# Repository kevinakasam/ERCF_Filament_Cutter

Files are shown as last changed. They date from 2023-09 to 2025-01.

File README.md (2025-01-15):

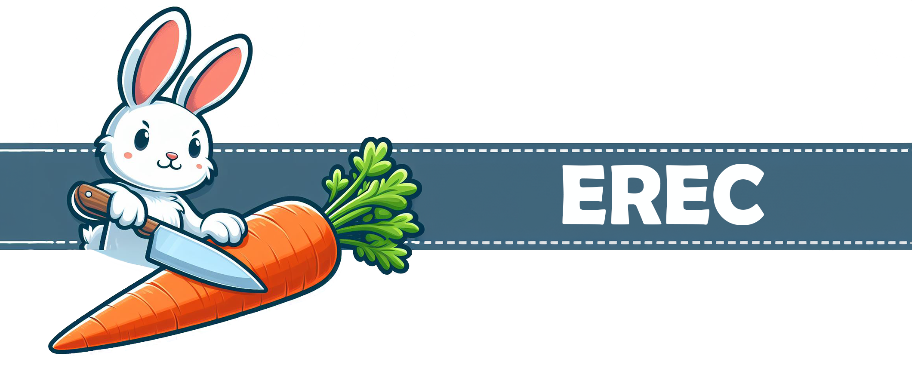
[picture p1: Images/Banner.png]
   

# Enraged Rabbit Encoder Cutter - Beta 7.0 🥕
<p align="center">
   &nbsp; 
   &nbsp;
   &nbsp;
</p>

### Attention! 
<strong> I’m not an expert and 3D printing is just my hobby. So please be careful when you build this mod and don’t just go ahead. All parts are tested and working. But everybody bears the risks of a modification him/herself! I'm not responsible if any harm occurs, so be careful, especially with the knife! </strong>

## Overview 

**[EREC](#erec)**<br>
**[BOM](#bom)**<br>
**[Assembly](#assembly)**<br>
**[Firmware](#firmware)**<br>
**[Changelog](#changelog--archive)**<br>
**[Showroom](#Showroom)**<br>
**[Acknowledgements](#Acknowledgements)**<br>

## EREC

This is a simple filament cutter for the awesome ERCF so tip tuning is less important.

It's made out of a Servo and a scalpell/exacto knife blade. The cutter get's mouted to the selector chart just behind the encoder - the cutter is basically an arm that swings to the left and right. Since the ECAS sits now on the Arm the filament path can be opened by swining the arm to the side. Then the ERCF can feed some filament mid air (*the filament tip*) and when the arm swings back to close the filament path the tip gets cut off by the knife on the arm. The cut off tip just falls off to the ground and the filament can be loaded with a clean tip the next time.

#### Why?
I never thought about a filament cutter untill I saw the [Filametrix](https://github.com/sorted01/Filametrix) design / got it recommended. Since I'm not using the ERCF with a Stealthburner (for now at least) I would have to make a cutter on my own. At the same time u/[BioKeks](https://github.com/BioCookieYT) requested a cutter for my Ender 3 fan duct ([Frankenstein 2.0](https://github.com/kevinakasam/FrankEnstein-Duct/tree/main/Frank2.0_Beta)) and that way I though we need something universial. After some days of tinkering this was the result - first with the MG90s servo, but that was so weak it was far aways from cutting it. So long speech short, thanks to [sorted01](https://github.com/sorted01) for the idea with the cutter!

#### Current Status
Considering my other ongoing [projects](https://kevinakasam.com/), I’ve decided to appoint u/[BioKeks](https://github.com/BioCookieYT) as the new primary contributor to this project. Don’t worry, I’m not completely stepping away, but if you have any questions, feel free to ask u/[BioKeks](https://github.com/BioCookieYT)!
<br>
<br>
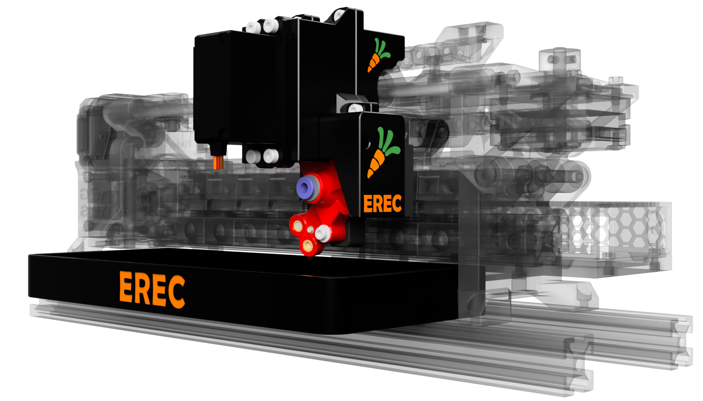
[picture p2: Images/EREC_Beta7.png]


## BOM
<table>
<tr>
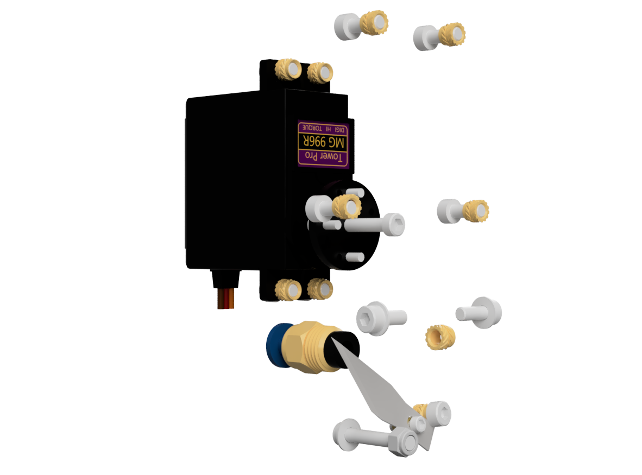
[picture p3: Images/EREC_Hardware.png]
EREC_Hardware
<td width=25%></td>
<td>
You can find the EREC BOM here. Make sure to gather all the required hardware before starting the assembly process ;)
<p>

[BOM](Doc/BOM.md) 
</td>
</tr>
</table>
<br>

## Assembly 

<table>
<tr>
<td>
The assembly process is straightforward; I’ve tried my best to keep it simple. If you need any help, feel free to join our discord server. 
<p>

[Documentation](Doc/EREC_BETA7.pdf) &nbsp;&nbsp; [Discord Server](https://discord.gg/Jw4frr64yV) &nbsp;&nbsp; [Discord Channel Link](https://discord.com/channels/964441223169449984/1169733100700434543)
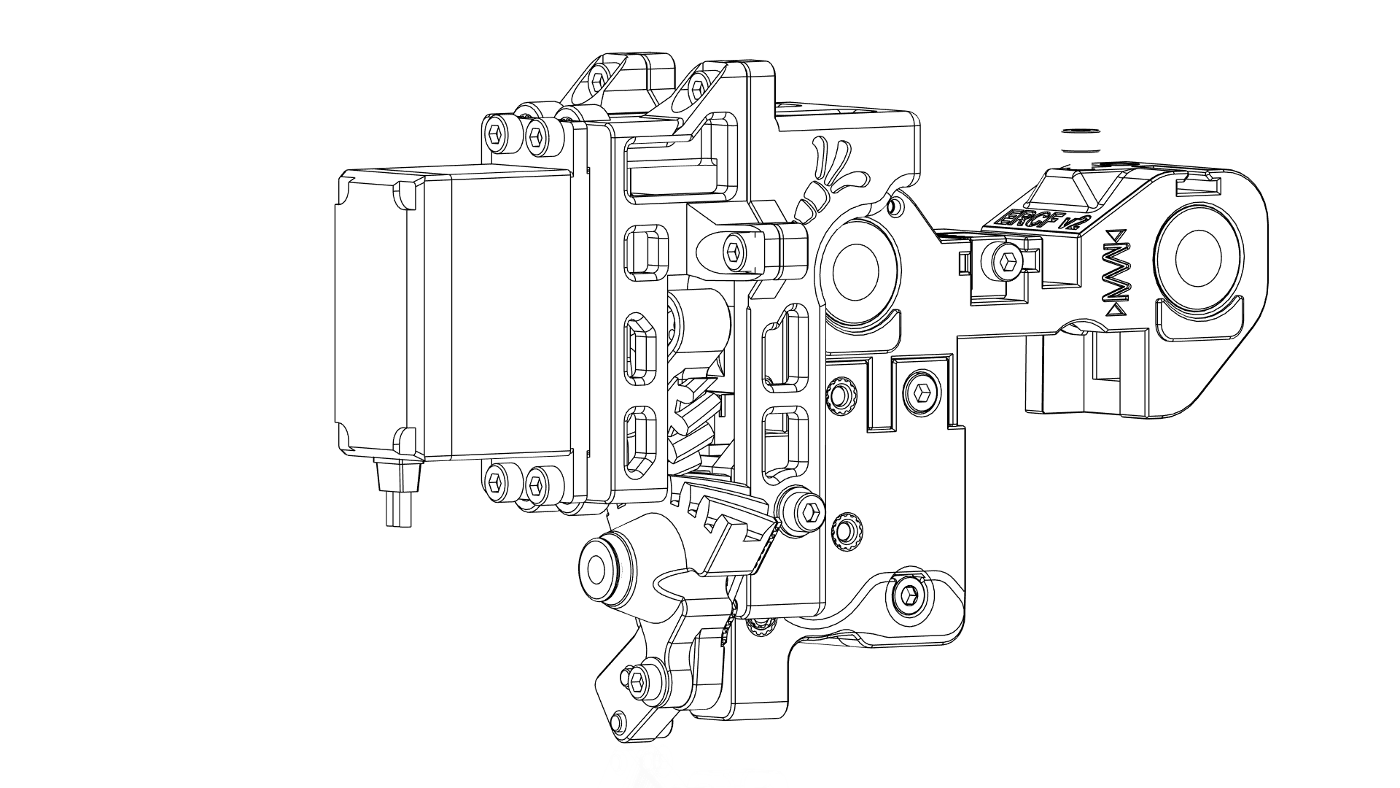
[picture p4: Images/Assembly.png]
<td width=35%></td>
</td>

</tr>
</table>

<br>

## Firmware
<table>
<tr>
<td width=20%>KlipperScreen</td>
<td>
EREC uses HappyHareV2 as its firmware. Thanks to maggieuk, you can enjoy easy integration as a third-party addon. For people using still ERCF-Software-V3, you can try the fork from u/ntchris. 

 [Happy Hare](https://github.com/moggieuk/Happy-Hare/wiki/Addon-Feature-Setup#---erec-filament-cutter) &nbsp;&nbsp; [ERCF-Software-V3 Fork](https://github.com/ntchris/ERCF-Software-V3)
</td>
</tr>
</table>

<br>

## Changelog & Archive
<table>
<tr>
<td>
EREC has undergone a long development process. Feel free to visit older revisions if you wish to explore its history 🥕
<p>

[Changelog](Doc/Changelog.md) &nbsp;&nbsp; [Archive](https://github.com/kevinakasam/ERCF_Filament_Cutter/tree/main/Archive) 
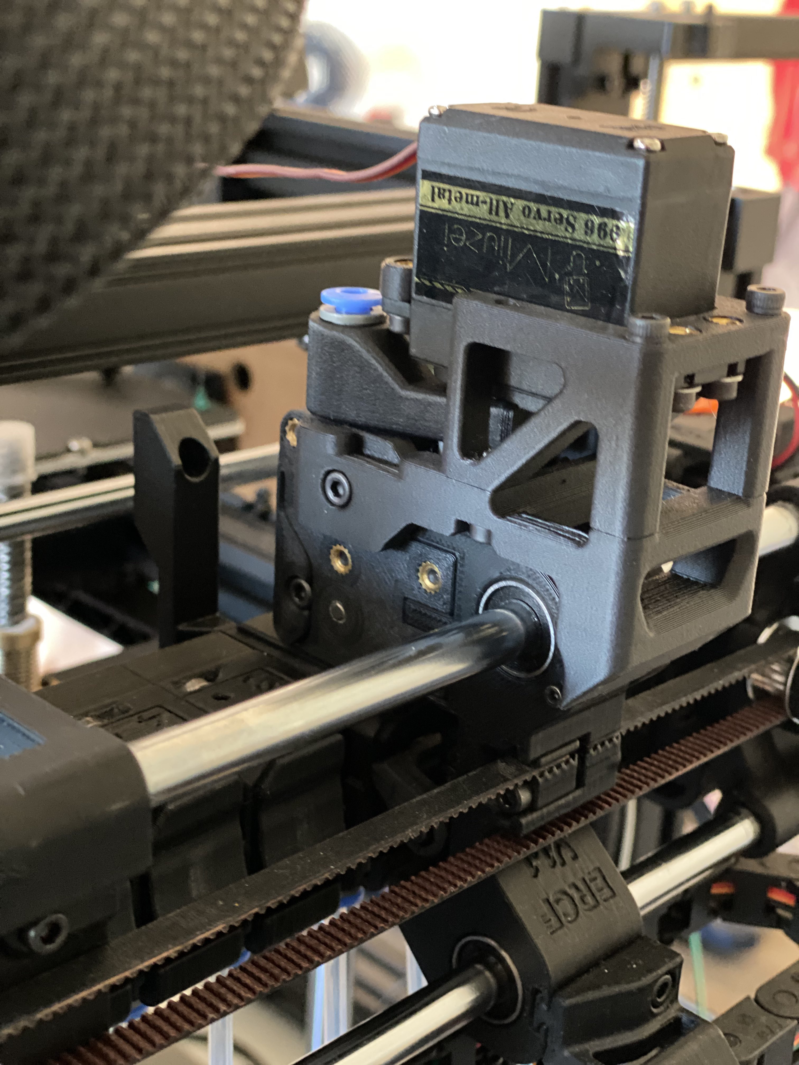
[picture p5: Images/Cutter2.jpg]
<td width=25%></td>
</td>

</tr>
</table>

<br>

## Showroom
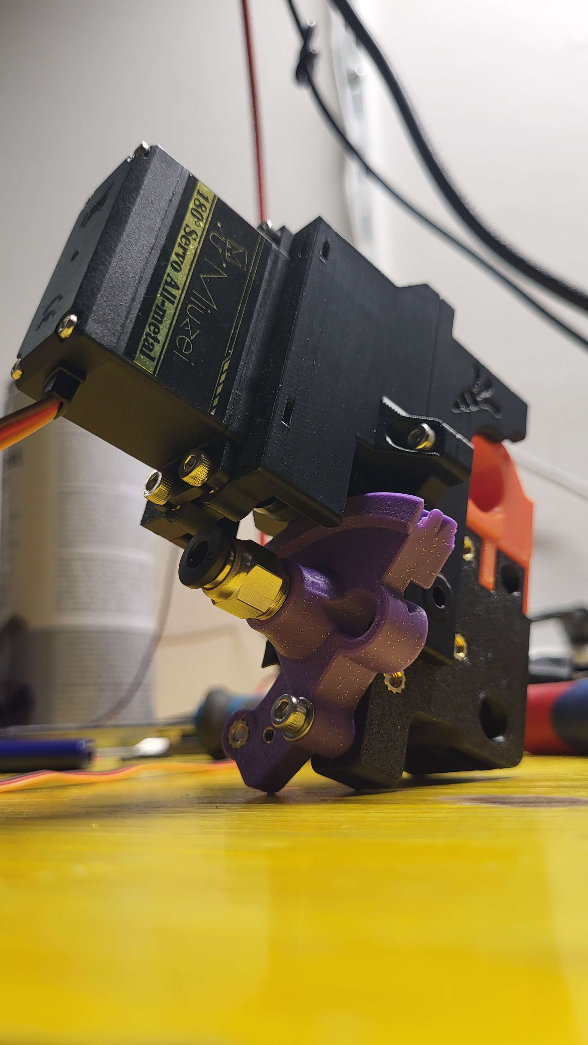
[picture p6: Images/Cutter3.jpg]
 

 #### Cutter Action (old version 😉):

<a href="http://www.youtube.com/watch?feature=player_embedded&v=-_qIqNOiTIw" target="_blank">
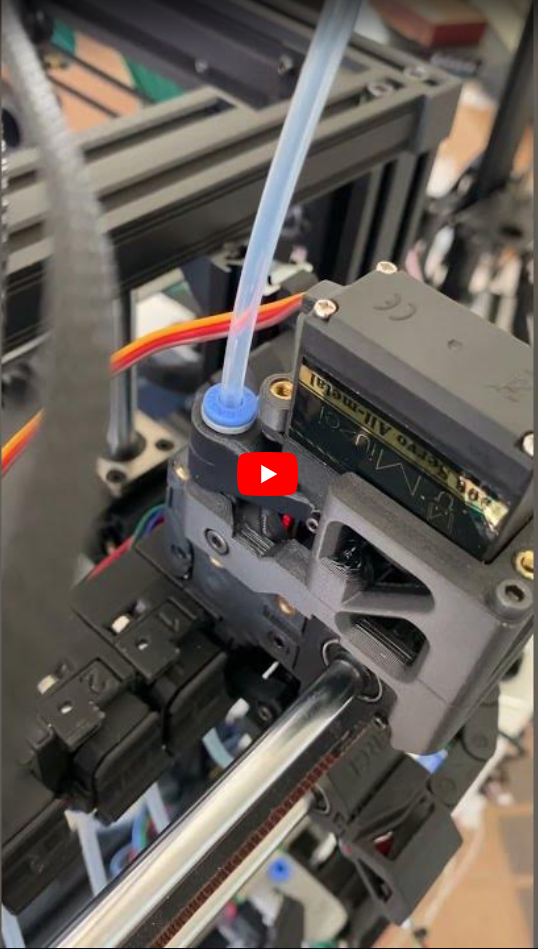
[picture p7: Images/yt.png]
Cutter Preview
  
</a>

## Acknowledgements
Thanks to...

-	[KevinAkaSam](https://kevinakasam.com/) – The magic guy who developed the first concept of EREC!
-	[BioKeks](https://github.com/BioCookieYT) – Developer of EREC Beta6 and Beta7
-	[xF4m3](https://github.com/xF4m3) – Thanks for helping with the Macros and tinkering with us
-	[sorted01](https://github.com/sorted01) – The guy behind Filametrix, thanks for the idea with the cutter!
-	[moggieuk](https://github.com/moggieuk) – Thanks a lot for awesome firmware and the quick help on the Voron Discord!
-	[HooiiooH](https://github.com/HooiiooH) and  [WiggyWooSaa](https://www.printables.com/de/@WiggyWooSaa_207419) – Thanks for the amazing mod ideas for Beta7 <3
-	[jmillerfo](https://www.printables.com/de/@jmillerfo_84104) – Unofficial developer of EREC Beta6.5 ;p, thanks a lot for some design ideas!
-	[jckennell](https://www.printables.com/de/@jckennell_470501) – Maker of the original Tip collector ;)
-	[ntchris](https://github.com/ntchris) – Thanks for making EREC compatible with ERCF-Software-V3
-	[comnmnor](https://github.com/nnaapp) - Thanks a lot for making EREC compatible with [Night Owl](https://github.com/kevinakasam/ERCF_Filament_Cutter/tree/main/Usermods/EREC%20For%20Nightowl)

And of course thanks to [EtteGit](https://github.com/EtteGit) and the amazing ERCFV2 Team for the awesome [EnragedRabbitProject](https://github.com/EtteGit/EnragedRabbitProject)!

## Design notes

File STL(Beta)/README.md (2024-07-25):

# EREC - Print Settings 🥕
Ensure your printer is well-tuned. Basic settings like EM, PA, and shrinkage should be calibrated. See more in this [guide](https://ellis3dp.com/Print-Tuning-Guide/).

- Material: ABS/ASA 
- 5 walls
- 55% cubic infill
- 5 top/bottom layers
- 0.20mm layer height except:

### `0.16mm [a] Cutter_Arm_XXX.stl`
- **Layer height: 0.16mm!!!**  
  The built-in supports won't work properly if printed with a 0.20mm layer height.

# `Cutter_Arm` Closed vs Open
There are two versions of the cutter arm: closed and open. From my testing, the main difference is how the tip behaves after it gets cut. With the open version, the tip flies to the right, while with the closed version, the tip flies toward the front.
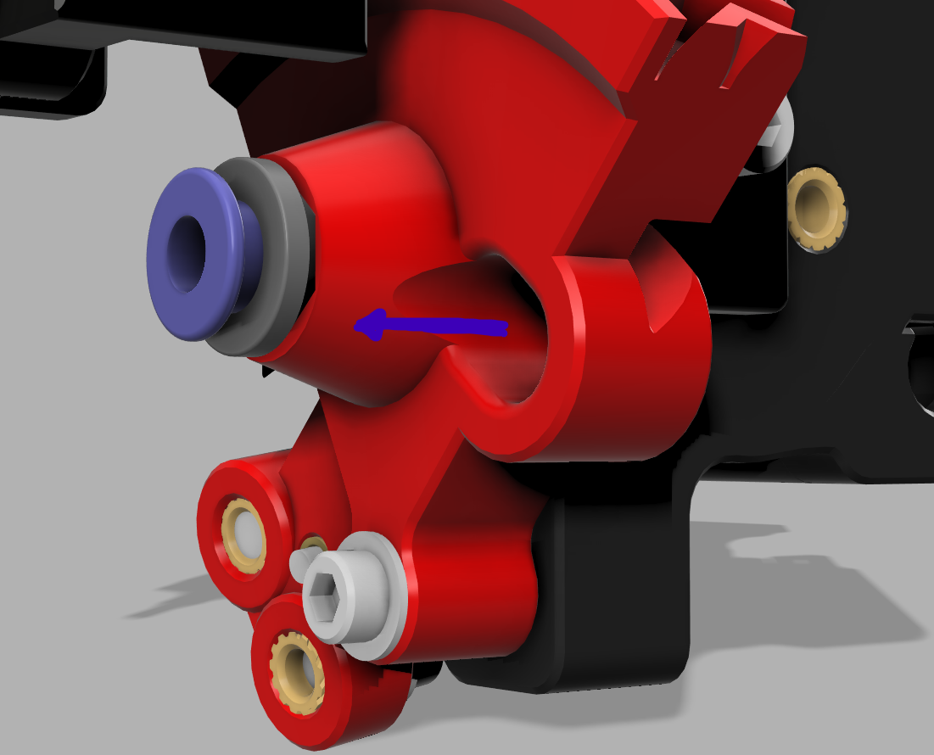
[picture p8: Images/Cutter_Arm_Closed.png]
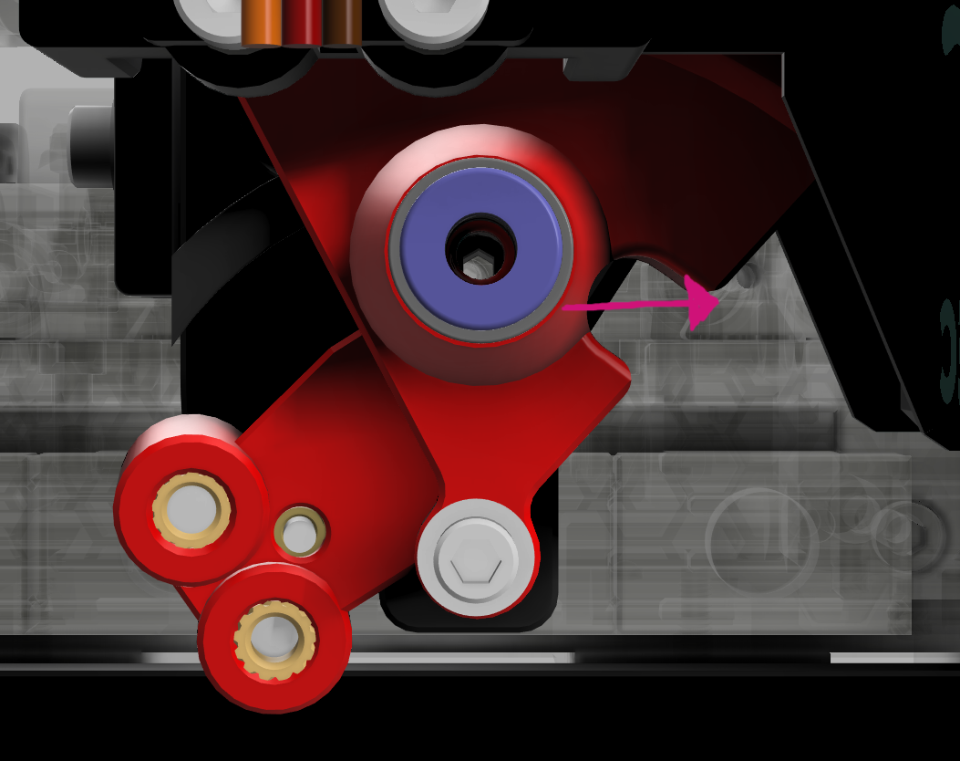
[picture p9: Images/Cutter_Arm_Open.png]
   

There is no better or worse version; it depends on your mounting solution which version you need. If you plan to use the tip collector, use the open version.

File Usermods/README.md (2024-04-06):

# EREC Mods  🥕
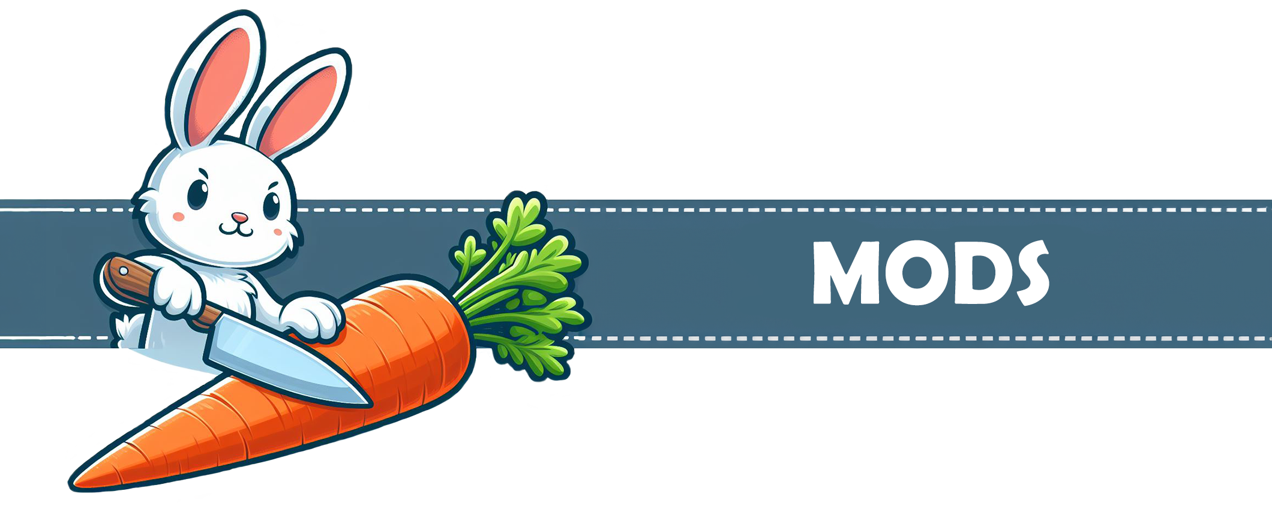
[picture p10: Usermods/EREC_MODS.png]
   

Welcome to the Usermods section of EREC, where you can find useful mods for the cutter. <br>
<strong>Note: I'm not responsible for the mods! This also means I am not responsible for keeping the mods updated, if something doesn't work, don't blame me. I will try my best to keep any mods compatible with the next versions of EREC. </strong>
## Rules

All mods should follow the [mod submission rules](https://github.com/VoronDesign/VoronUsers/wiki/Mod-Submission-Rules) from the VORON Design team, the folder structure should be similar to EREC: 

    └── Usermods/
        └──YourUsername/
            ├── ModName/
            │   ├── STL/
            │   │   ├── [a]_accent_part.stl
            │   │   └── non_accent_part.stl
            │   ├── CAD/
            │   │   ├── step_file.step
            │   ├── Images/
            │   │   ├── ...
            │   ├── Doc/
            │   │   └── ...
            │   ├── README.md
            └── ModName2/
                ....

You don't have to be fancy with the Readme, add a little description, BOM, some images and if needed some assembly instructions. You can find a template [here](https://github.com/kevinakasam/ERCF_Filament_Cutter/edit/main/Doc/template.md). 

## Pull requests, WHAT?
It's not a problem in case you don't know how all the GitHub stuff works! Hit BioKeks up on Discord, we will find a solution ;)

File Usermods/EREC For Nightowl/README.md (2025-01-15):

## Required Hardware 🥕
* 6x3mm Magnets x4 : Tip catcher tray and dock
* Nightowl BOM Countersunk Magnets x4 : Reused from Nightowl BOM for magnetic EREC cover
* M3x6mm BHCS or SHCS : Mounting cover main body to adapter plate
* __EREC BOM Hardware!__

## Instructions 🥕
The descriptions of where the magnets/screws are used above + the CAD file included should be sufficient. Use the EREC instructions to build it, and refer to the CAD/above to install the adapter on the Nightowl.

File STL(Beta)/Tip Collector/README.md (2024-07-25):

# Tip Collector - Based on jckennell's mod

You can find various sizes for the Tip Bin in the folder. If you need a custom size, you can create one using the parametric CAD  thanks to @[KevinAkaSam](https://kevinakasam.com/).

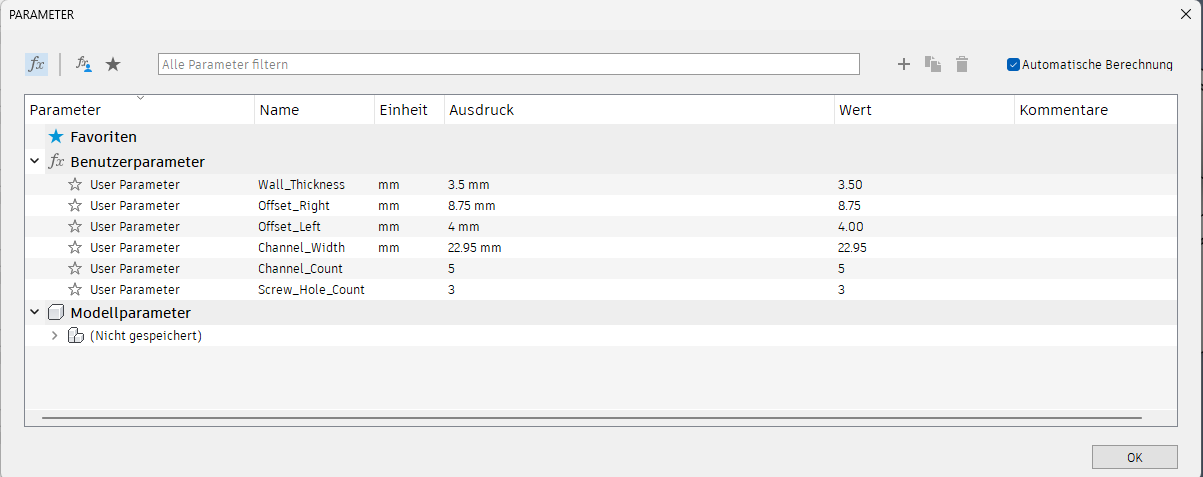
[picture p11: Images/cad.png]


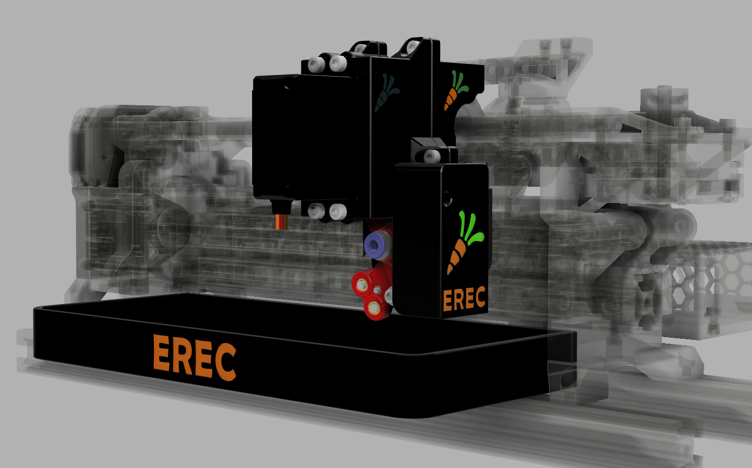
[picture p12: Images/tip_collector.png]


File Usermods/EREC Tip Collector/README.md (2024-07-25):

#
# Beta 6.0 Mod! You can find the official tip collector based on this mod in the STLs. 

# EREC Tip Collector - jckennell 🥕
This is a simple deflector shroud and catch tray for filament tips cut off by the Enraged Rabbit Encoder Cutter.

   

# STLs
You can find the newest files [here](https://www.printables.com/de/model/777877-erec-tip-collector) 🥕

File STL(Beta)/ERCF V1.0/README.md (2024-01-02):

Just print the latest Beta files.

Note: You can choose from:

1. Stock Encoder or Binky.
2. Springy or Stock Selector

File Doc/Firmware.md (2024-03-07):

# Firmware 🥕

I'm using the awesome [Happy Hare](https://github.com/moggieuk/Happy-Hare) firmware for the ERCF. I'm sure this also works with the stock macros, but I haven't tried that. In addition, the Happy Hare `[mmu_servo]` works a lot better than the stock `[servo]` from Klipper.

<br>

## Happy Hare V2.5 or newer

With [Happy Hare](https://github.com/moggieuk/Happy-Hare) 2.5 EREC became an official addon of the firmware. It is highly recommended setting EREC up this way, you can find more information [here](https://github.com/moggieuk/Happy-Hare/tree/main/config/addons#config)

<br>
<br>

## Older Versions (deprecated)

#### Changes to mmu_software.cfg

If the `[gcode_macro _MMU_POST_UNLOAD]` section isnt yet defined in your `mmu_sotware.cfg` simply copy the whole following block into the file (there's already a section with un-loading macros). If it's already there just paste the `CUTTER_ACTION` Macro there

```
# Callback macros for modifying Happy Hare behavour
# This occurs after unloading filament on a toolchange
#
# This can be used for the Filament Cutter
# Note that restoration to original toolhead position is ensured by Happy Hare.
#
[gcode_macro _MMU_POST_UNLOAD]
description: Optional post unload routine for filament change
gcode:
    CUTTER_ACTION
```

#### Cutter config

Add this to your config. I added a file named `mmu_ercf_cutter.cfg` in the ` /config/mmu/optional` to implement it with a `[include mmu/optional/mmu_ercf_cutter.cfg]`.
Note: The Macros aren't done yet ~~and aren't working as expected~~.

```
[mmu_servo cut_servo]         #`mmu_servo` only for the Happy Hare firmware, otherwise only `servo`
pin: mmu:PA7                  #Extra Pin on the ERCF easy Board
maximum_servo_angle: 180      #Set this to 60 for a 60° Servo
minimum_pulse_width: 0.0005   #Adapt these for your servo
maximum_pulse_width: 0.0025   #Adapt these for your servo

[gcode_macro _CUT_VAR]
description: Empty macro to store the variables

### Servo ###
variable_servo_closed_angle: 70          #Adapt these for your setup
variable_servo_open_angle: 10            #Adapt these for your setup
variable_servo_blocked_angle: 40         #I have the idea to home the filament against the cutter by blocking the filament path with 1/2 of the servo rotation. Could make cuts more precise
variable_servo_idle_time: 500            #Time to let the servo reach it's position, in milliseconds (1 second = 1000 milliseconds)

### Feed length
variable_feed_length: 48                 #Rough estimation of the parking position to the outside of the encoder
variable_cut_length: 10                  #How much you want to cut off in mm
variable_cut_amount: 1                   #Number of times the cutter tries to cut the filament

gcode:

[gcode_macro CUTTER_CLOSE]
description: Set Servo in the close position
gcode:
    {% set cutvar = printer["gcode_macro _CUT_VAR"] %}
    SET_SERVO SERVO=cut_servo ANGLE={cutvar.servo_closed_angle}
    SET_SERVO SERVO=cut_servo WIDTH=0.0
    G4 P{cutvar.servo_idle_time}
    M118 Cutter closed
    M400
    G4 P0

[gcode_macro CUTTER_OPEN]
description: Set Servo in the open position
gcode:
    {% set cutvar = printer["gcode_macro _CUT_VAR"] %}
    SET_SERVO SERVO=cut_servo ANGLE={cutvar.servo_open_angle}
    SET_SERVO SERVO=cut_servo WIDTH=0.0
    G4 P{cutvar.servo_idle_time}
    M118 Cutter open
    M400
    G4 P0

[gcode_macro CUTTER_BLOCK]
description: Set Servo in the blocked position
gcode:
    {% set cutvar = printer["gcode_macro _CUT_VAR"] %}
    SET_SERVO SERVO=cut_servo ANGLE={cutvar.servo_blocked_angle}
    SET_SERVO SERVO=cut_servo WIDTH=0.0
    G4 P{cutvar.servo_idle_time}
    M118 Cutter blocked
    M400
    G4 P0

# New Cutter Action Macro - thanks to xF4m3 and moggieuk <3
[gcode_macro CUTTER_Action]
description: Set Servo in the close position. Doesn't work properly yet.
gcode:
    {% set cutvar = printer["gcode_macro _CUT_VAR"] %}
    
    CUTTER_OPEN
    MMU_TEST_MOVE MOVE={cutvar.feed_length + cutvar.cut_length}
    {% for i in range(cutvar.cut_amount) %}
      CUTTER_CLOSE
      CUTTER_OPEN
    {% endfor %}
    MMU_TEST_MOVE MOVE=-1
    CUTTER_CLOSE
    
   _MMU_STEP_SET_FILAMENT STATE=1 
   _MMU_STEP_UNLOAD_GATE
   
    M400
    G4 P0

## Old Cutter Action Macro
#[gcode_macro CUTTER_Action]
#description: Set Servo in the close position. Doesn't work properly yet.
#gcode:
#    {% set cutvar = printer["gcode_macro _CUT_VAR"] %}
#
#    MMU_SERVO POS=down
#    CUTTER_OPEN
#    MMU_TEST_MOVE MOVE={44 + cutvar.cut_length} #Rough estimation of the parking position to the outout of the encoder + the cut length
#    CUTTER_CLOSE
#    CUTTER_OPEN
#    CUTTER_CLOSE
#    CUTTER_OPEN
#    MMU_TEST_MOVE MOVE=-1
#    CUTTER_CLOSE
#    MMU_EJECT
#    #MMU_SERVO POS=down
#    M400
#    G4 P0
```

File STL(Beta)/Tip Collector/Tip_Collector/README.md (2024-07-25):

# Tip Collector - Based on jckennell's mod

### Please check if the size matches your ERCF build!

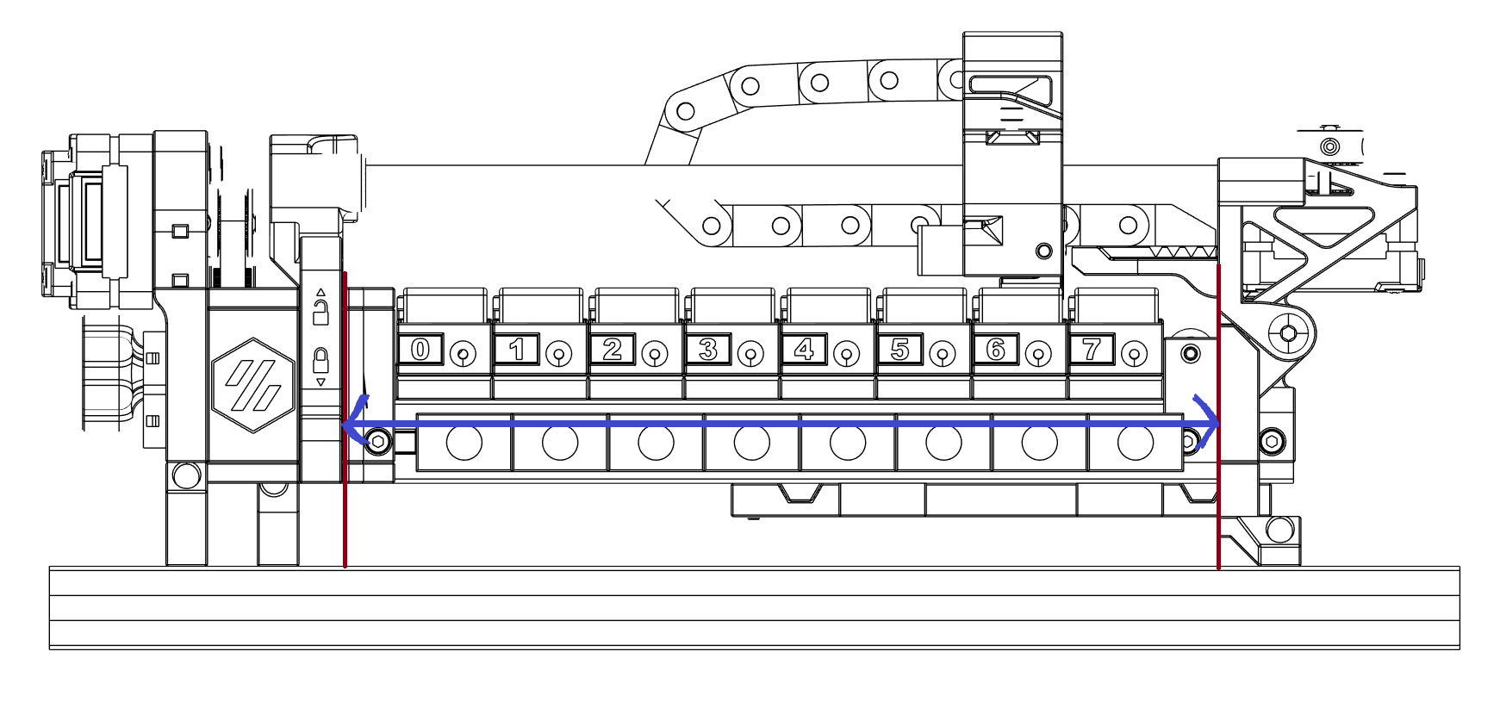
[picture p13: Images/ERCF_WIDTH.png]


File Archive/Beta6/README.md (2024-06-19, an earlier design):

   

# Enraged Rabbit Encoder Cutter - Beta 6.0 🥕
<p align="center">
   &nbsp; 
   &nbsp;
   &nbsp;
</p>

### Attention!
<strong> I’m not an expert and 3D printing is just my hobby. So please be careful when you build this mod and don’t just go ahead. All parts are tested and working. But everybody bears the risks of a modification him/herself! I'm not responsible if any harm occurs, so be careful, especially with the knife! </strong>

## Overview

**[EREC](#erec)**<br>
**[BOM](#bom)**<br>
**[Assembly](#assembly)**<br>
**[Firmware](#firmware)**<br>
**[Showroom](#user-print-showroom)**<br>
**[Acknowledgements](#acknowledgements)**<br>
**[Changelog](#changelog)**<br>
## EREC

This is a simple filament cutter for the awesome ERCF so tip tuning is less important.

It's made out of a Servo and a scalpell/exacto knife blade. The cutter get's mouted to the selector chart just behind the encoder - the cutter is basically an arm that swings to the left and right. Since the ECAS sits now on the Arm the filament path can be opened by swining the arm to the side. Then the ERCF can feed some filament mid air (*the filament tip*) and when the arm swings back to close the filament path the tip gets cut off by the knife on the arm. The cut off tip just falls off to the ground and the filament can be loaded with a clean tip the next time.

#### Why?
I never thought about a filament cutter untill I saw the [Filametrix](https://github.com/sorted01/Filametrix) design / got it recommended. Since I'm not using the ERCF with a Stealthburner (for now at least) I would have to make a cutter on my own. At the same time u/[BioKeks](https://github.com/BioCookieYT) requested a cutter for my Ender 3 fan duct ([Frankenstein 2.0](https://github.com/kevinakasam/FrankEnstein-Duct/tree/main/Frank2.0_Beta)) and that way I though we need something universial. After some days of tinkering this was the result - first with the MG90s servo, but that was so weak it was far aways from cutting it. So long speech short, thanks to [sorted01](https://github.com/sorted01) for the idea with the cutter!

#### Current Status
Considering my other ongoing [projects](https://kevinakasam.com/), I’ve decided to appoint u/[BioKeks](https://github.com/BioCookieYT) as the new primary contributor to this project. Don’t worry, I’m not completely stepping away, but if you have any questions, feel free to ask u/[BioKeks](https://github.com/BioCookieYT)!
<br>
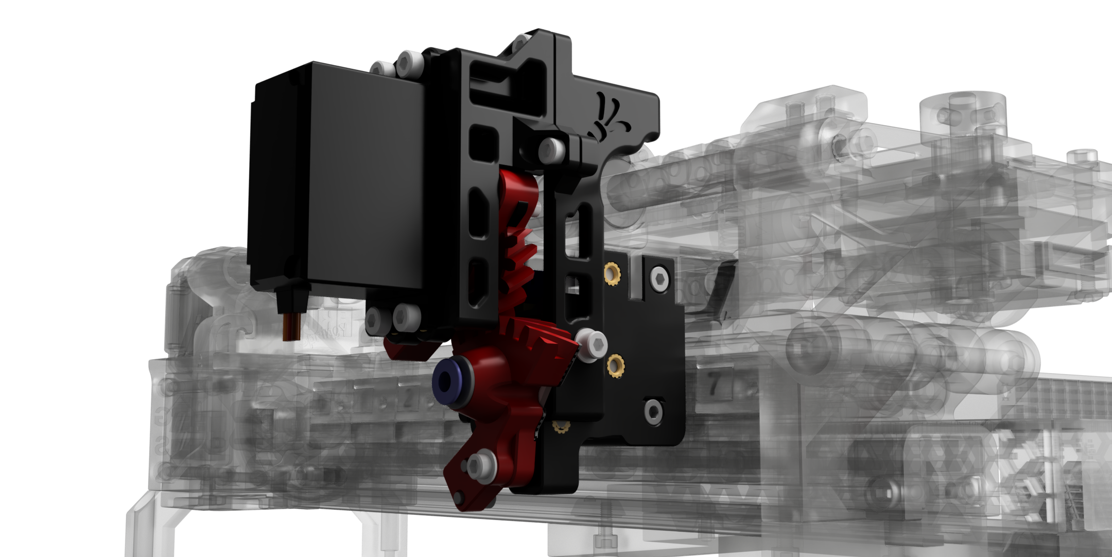
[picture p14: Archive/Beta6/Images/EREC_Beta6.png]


### BOM
| **Qty** | **Part** | **Description** |
|:---:|:---:|:---:|
| 1 | [Servo MR996](https://amzn.eu/d/gEQACnZ) | That's just the servo I use, nothing special. But the MG90S are definetly too weak. 60° may work, but I highly recommend getting at least a 90° servo. Also check the torque, u/[BioKeks](https://github.com/BioCookieYT) was't able to cut soft PLA with a 12kg.cm servo |
| 1 | [Exacto knife blade No. 11](https://amzn.eu/d/0ZmUXIy) | That's just an example so you know the shape/type. Higher quality blades probably last longer. |
| 1 | [5V buck converter](https://de.aliexpress.com/item/32730909898.html) | The Servo can take quite a lot of current, enough to shut down my ERCF board. If you have the same problem try a buck converter wired to the PSU or use your dedicated 5V PSU |
| 10 | M3 Threaded Insert | Just the same inserts you already used during the ERCF assembly 😉 |
| 1 | M3 lock nut | To prevent the screw on the cutter_arm to be loosened over time |
| 3 | M3 washer | Use some washers to screw in the cutter_arm and the servo_hinge_mount |
| 1 | M3x18 SHCS | Used to mount the cutter arm |
| 4 | M3x6 SHCS | These are used to mount the servo motor on the printed part |
| 1 | M3x6 BHSC | This screw comes usually with your servo motor, its used to mount the servo_arm on the servo. SHCS probably works also |
| 2 | M2.5x6 SHCS | To mount the knife to the arm you will need some M2.5 screws, it doesn't matter if they are longer than 6mm. Pro tip: Check out your hotend assembly kit, it often ships with some M2.5 screws |
| 4 | M2x6 SHCS | These screws are used to lock the servo attachment with the printed part. Screw length can vary a bit, if you don't have any laying around I recommend getting a cheap M2-Screw kit on AliExpress |

## Assembly

<table>
<tr>
<td>
The assembly process is straightforward; I’ve tried my best to keep it simple. If you need any help, feel free to join our discord server. 
<p>

[Assembly](Doc/EREC_Assembly.pdf) &nbsp;&nbsp; [Discord Server](https://discord.gg/Jw4frr64yV) &nbsp;&nbsp; [Discord Channel Link](https://discord.com/channels/964441223169449984/1169733100700434543)
<td width=35%></td>
</td>

</tr>
</table>

<br>

## Firmware
<table>
<tr>
<td width=20%>HHv2</td>

<td>
EREC uses the awesome Happy Hare firmware for the ERCF. I'm sure this also works with the stock macros, but I haven't tried that. In addition, the Happy Hare <code>[mmu_servo]</code> works a lot better than the stock <code>[servo]</code> from Klipper.

<p>

[Macros](Doc/Firmware.md) &nbsp;&nbsp; [Happy Hare](https://github.com/moggieuk/Happy-Hare/blob/main/doc/ercf_v2.md)
</td>
</tr>
</table>

<br>

## Acknowledgements
Thanks to...

* [BioKeks](https://github.com/BioCookieYT) for tinkering with me! Luckily we both got the ERCF roughly at the same time :D

* [xF4m3](https://github.com/xF4m3) for the Macro help!

* [sorted01](https://github.com/sorted01) for the idea with the cutter!

* [moggieuk](https://github.com/moggieuk) for the [awesome firmware](https://github.com/moggieuk/Happy-Hare/tree/23604442613be6bbbc8c70f57ff55fe65b1268e4) and the quick help on the Voron Discord!

And of course thanks to [EtteGit](https://github.com/EtteGit) and the amazing ERCFV2 Team for the awesome [EnragedRabbitProject](https://github.com/EtteGit/EnragedRabbitProject)!

### Showroom 

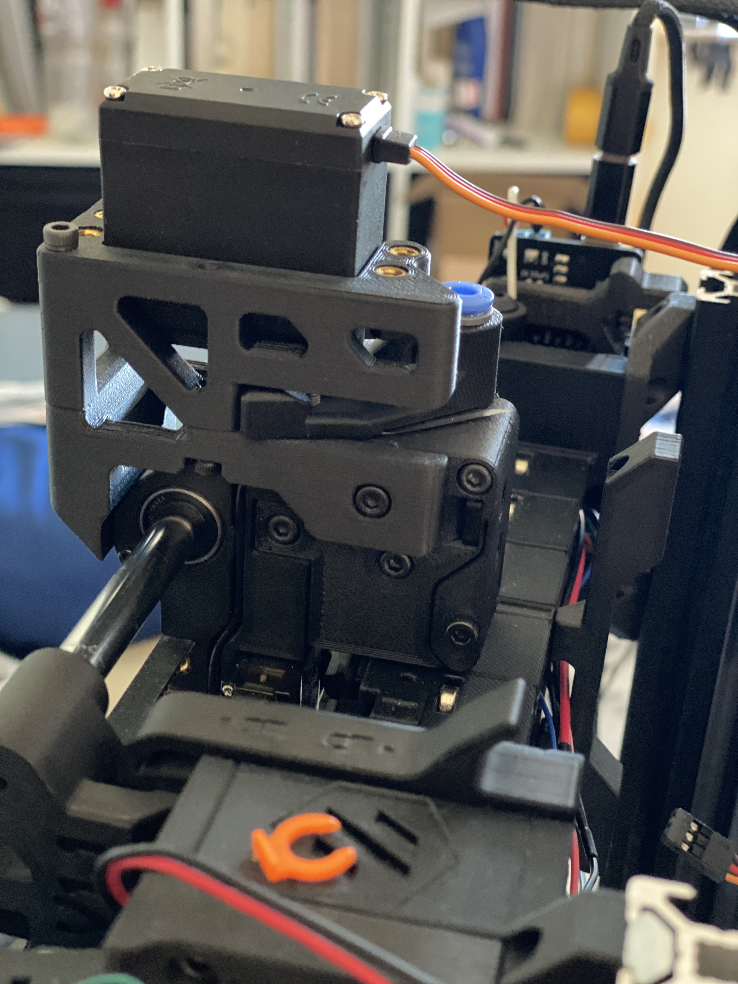
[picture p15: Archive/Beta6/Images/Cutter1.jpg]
   

 #### Cutter Action:
 
<a href="http://www.youtube.com/watch?feature=player_embedded&v=-_qIqNOiTIw
" target="_blank">Cutter Preview</a> 

### Changelog

#### 30/09/2023: Binky Support
- Adaption of the Binky encoder for the cutter - made by u/[BioKeks](https://github.com/BioCookieYT)
- Fixed an overhang issue with the `Servo_Mount.stl`

#### 01/10/2023: [Triple-Decky](https://github.com/gneu42/Triple-Decky/tree/main) Support
- Adaption of the Binky encoder for the 3PS version - made by u/[BioKeks](https://github.com/BioCookieYT)

#### 10/10/2023: Bowden Tube Adjustment
- Improved bowden tube fit by adjusting the encoder - Thanks for the feedback u/[xF4m3](https://github.com/xF4m3)  
- Fixed an overhang issue with the `Encoder_Cart_Left.stl` - made by u/[BioKeks](https://github.com/BioCookieYT)

#### 03/11/2023: Beta5 Release
- Overhauled the cutter design for more cutting power and reliability
- Adaption of the Binky encoder for Beta5 - made by u/[BioKeks](https://github.com/BioCookieYT)

#### 23/12/2023: ERCF2.0 Release
- Adaption for the new ERCF2.0 Encoder - made by u/[BioKeks](https://github.com/BioCookieYT)

#### 15/02/2024: Beta6 Release
**NOTE: Beta6 drops support for the old ERCFV1**
- [Changelog for Beta6](https://github.com/kevinakasam/ERCF_Filament_Cutter/blob/main/Doc/Beta6_Changes.md)

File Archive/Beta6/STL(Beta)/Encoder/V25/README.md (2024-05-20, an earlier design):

# Hey! 🥕

This experimental version of the V25 V-Bearing encoder includes fixes for filament path issues and features the heatset insert modification from HooiiooH. Feel free to leave some feedback on the discord server! 

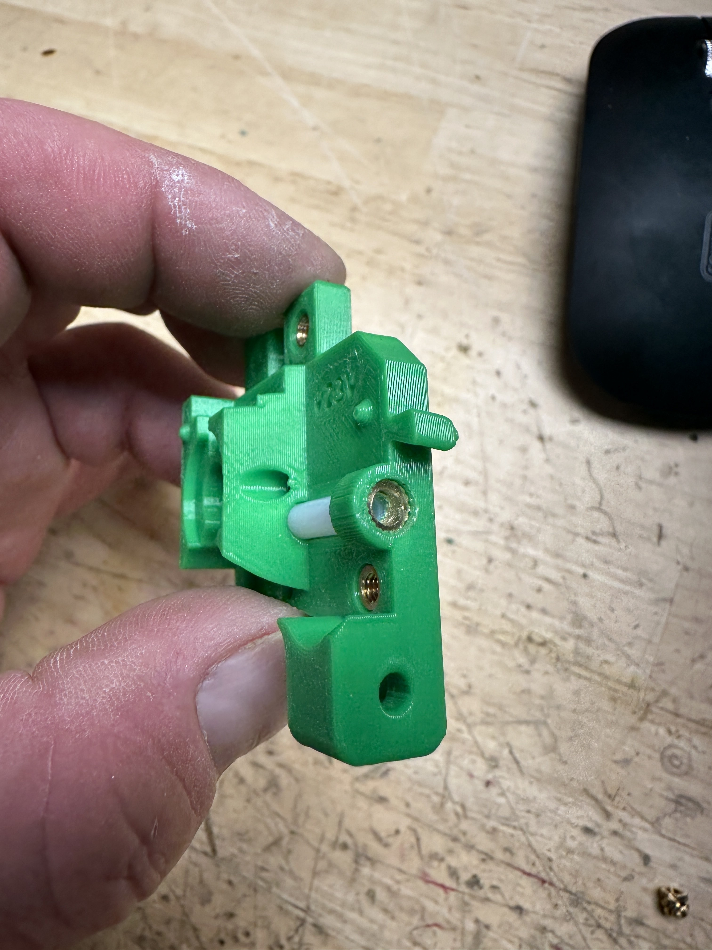
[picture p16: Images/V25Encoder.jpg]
 

(image from gsx8299 🥕)

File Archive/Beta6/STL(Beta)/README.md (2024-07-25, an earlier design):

Note: Beta6 no longer supports ERCFV1, please use instead [Beta5]([https://github.com/kevinakasam/ERCF_Filament_Cutter/tree/main/Archive/STLs/ERCF%20V1.0) or try out this mod https://github.com/kevinakasam/ERCF_Filament_Cutter/issues/12 😉

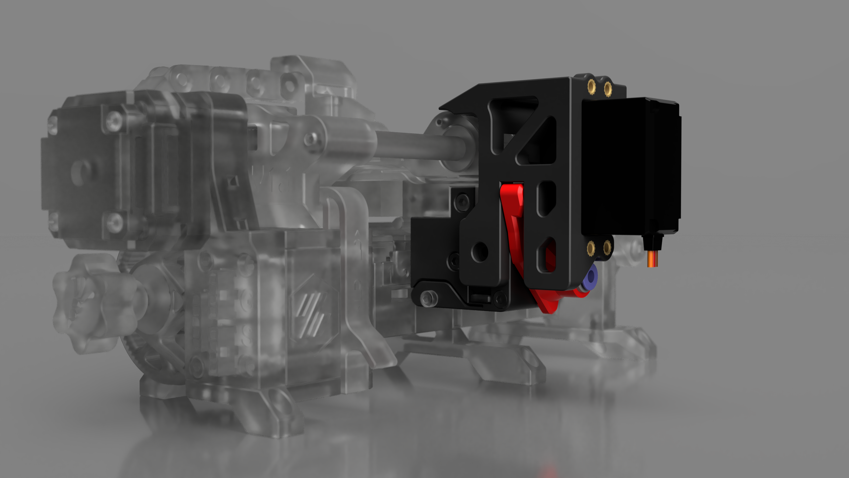
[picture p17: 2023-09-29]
Images/Render.png

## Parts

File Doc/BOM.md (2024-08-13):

# EREC - KITs 🥕

As EREC has gained popularity, some vendors have started offering kits, making it much easier to source parts. 😉

### Official Tested Kits:
- Seleadlab Store - [Link](https://s.click.aliexpress.com/e/_opGhKz5 ) (Affiliate) <br> 

<br><br>

<strong> Disclaimer:</strong> The kits are provided by third-party vendors, and I do not endorse or guarantee their quality, safety, or compliance with any legal standards. Any issues or disputes arising from the purchase or use of these kits should be addressed directly with the respective vendor. By using these kits, you acknowledge that I am solely the designer of EREC and not involved in the manufacturing, distribution, or sale of these products.
<br><br>

<strong> Affiliate Disclosure: </strong> Some of the links in this README are affiliate links. This means that if you click on a link and purchase a product, I may receive a commission at no additional cost to you. This helps support my work on EREC.

# BOM 🥕 

| Qty | Part | Description |
|-----|---|---|
| 1 | [**180° Servo MR996**](https://www.amazon.de/dp/B0C1TXW74L?psc=1) | This is the servo I use, nothing special, but MG90S servos are definitely too weak. Ensure the servo has a rotation range of **180 degrees**! Check the torque; u/BioKeks wasn't able to cut soft PLA with a 12kg.cm servo. |
| 1 | [5V Buck Converter](https://www.amazon.de/-/en/Converter-Step-Down-Regulator-Adjustable-Downward/dp/B0D7BWSTCX/) | Prevents the ERCF board shutdown caused by the servo's high current draw. Can be wired to the PSU or used with a dedicated 5V PSU. |
| 1 | [Exacto Knife Blade No. 11](https://www.amazon.de/dp/B0757LKXRV?ref_=cm_sw_r_cp_ud_dp_B652AFBS86TT6F6YTZJ2) | Example shape/type for reference. Higher quality blades are recommended for longer-lasting performance. |
| - | Wire to Extend Servo Motor Cable | Use any cable you have on hand to extend the servo wire, as it is too short. Ensure the wire can handle the peak current of the servo motor. |
| 1 | Round Servo Horn | To mount the Servo Gear to the servo. |
| 4+  | Zip Ties | Same zip ties used during the ERCF assembly. |
| 1 | ECAS or PC4-M10 | Choose based on preference; both versions of the cutter arm are provided. |
| 12  | M3 Threaded Insert | Same inserts used during the ERCF assembly. |
| 1 | M2 Threaded Insert (3.2 OD) | Inserting these can be tricky, take your time. 😉 |
| 1 | M3 Lock Nut | Prevents the screw on the cutter arm from loosening over time. |
| 5 | M3 Washer | Used for securing the cutter arm and the servo hinge mount. |
| 1 | M3x18 SHCS | Screw used to mount the cutter arm. |
| 6 | M3x6 SHCS | Used at multiple mounting points. |
| 1 | M2x6 SHCS | Used to mount the knife to the cutter arm. |

<br>

# Tip Collector - BOM 🥕 

| Qty | Part | Description |
|-----|---|---|
| 2 | M2x6 SHCS | Used to mount the tip catcher |
| 2 | M2 Threaded Insert (OD 3.2) | Inserting those can be tricky, take your time 😉  . |
| 3 | M3x8 SHCS | Used to mount the Tip Bin |
| 3 | M3 T-Nut | Used to 2020 profile mounting |

<br>
<br>
<br>


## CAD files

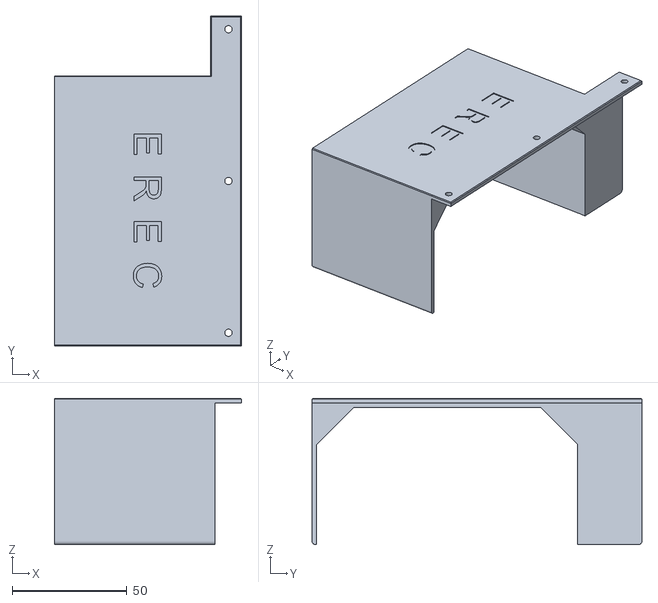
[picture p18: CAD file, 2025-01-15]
Usermods/EREC For Nightowl/STLs/Cover_Main_Body.stl
81.5 x 143.6 x 63.7

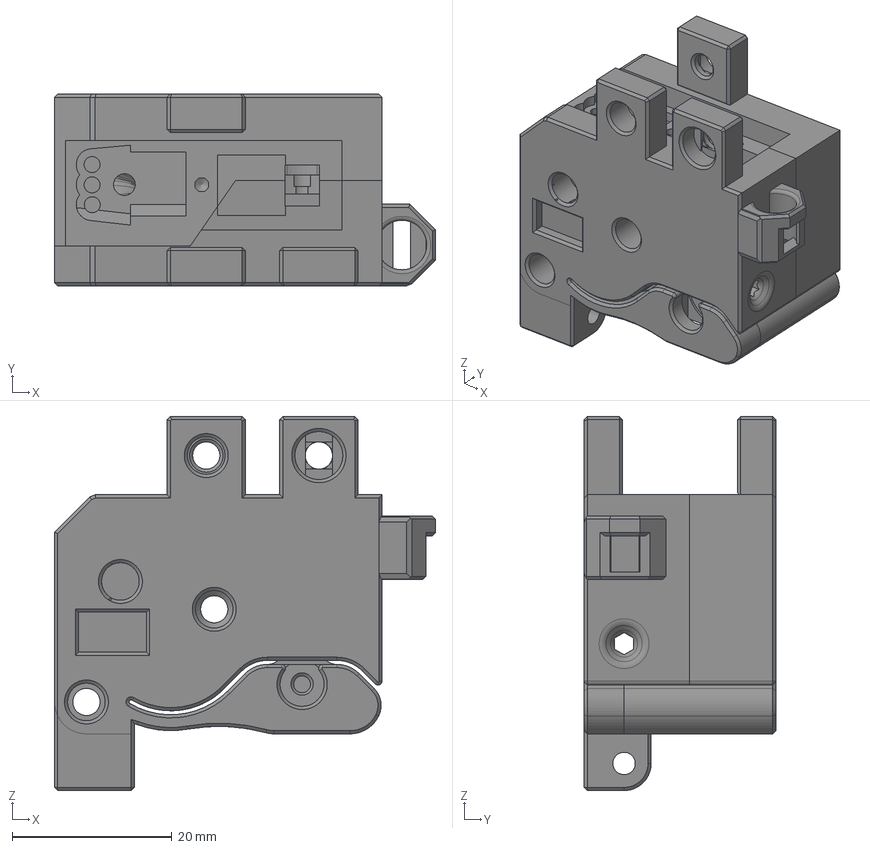
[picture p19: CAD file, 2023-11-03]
CAD/BinkyFilamentCutter_beta5.0.step
47.7 x 24.0 x 46.8 mm
Encoder_Right_With_Magnets
Encoder_Right
Encoder_Left (1)

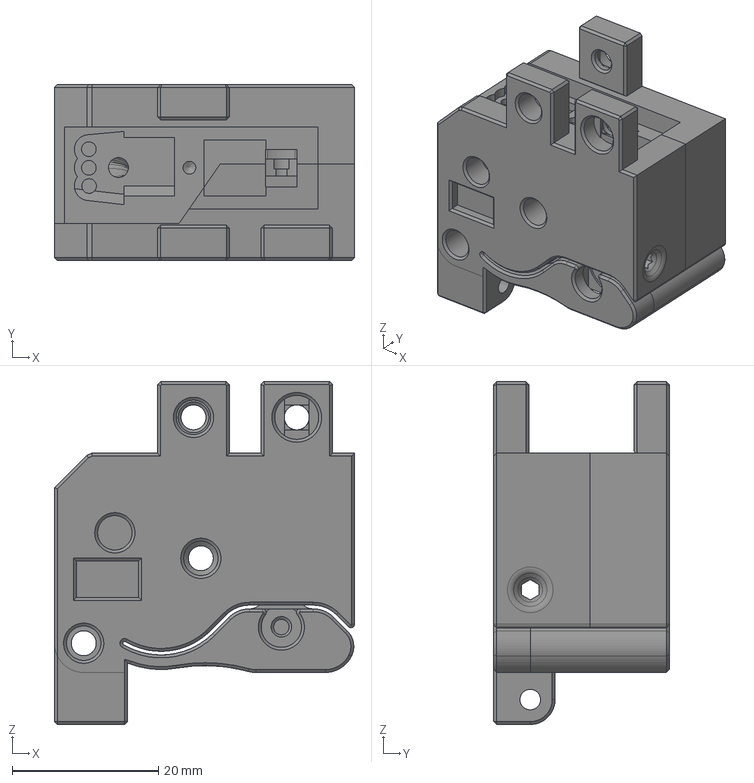
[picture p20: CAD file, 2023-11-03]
CAD/ERFC V1.0/BinkyFilamentCutter_beta5.1.step
41.0 x 24.0 x 46.8 mm
Encoder_Left (1)
Encoder_Right

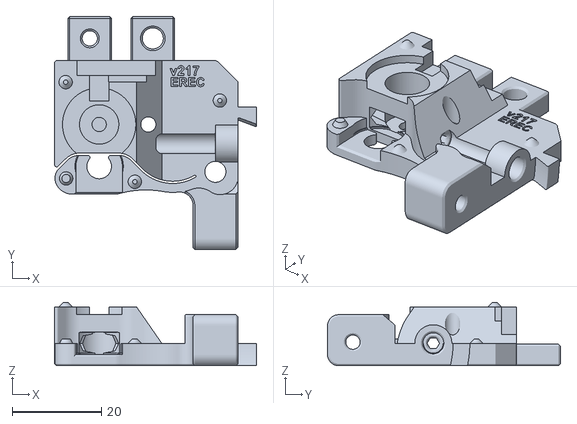
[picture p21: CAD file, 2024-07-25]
STL(Beta)/Encoder/623-Bearing/623Encoder_Right.stl
45.2 x 52.1 x 14.2

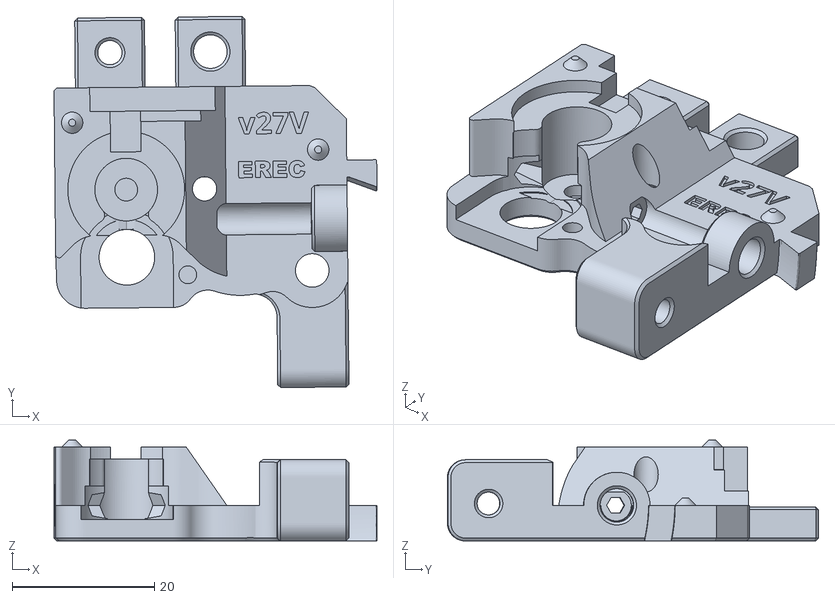
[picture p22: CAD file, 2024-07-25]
STL(Beta)/Encoder/V-Bearing/VEncoder_Right.stl
45.3 x 52.1 x 14.2

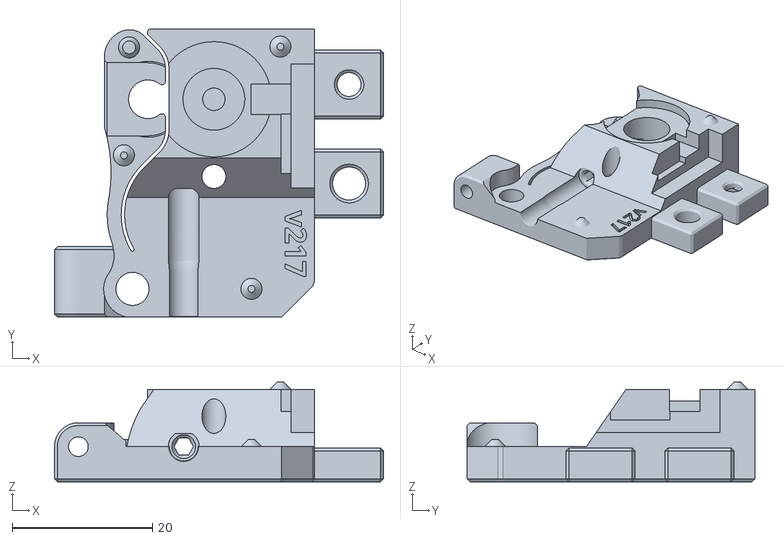
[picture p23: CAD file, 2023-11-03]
STL(Beta)/ERCF V1.0/Beta5.2/Encoder/Binky_Encoder_Right.stl
46.8 x 41.0 x 14.2

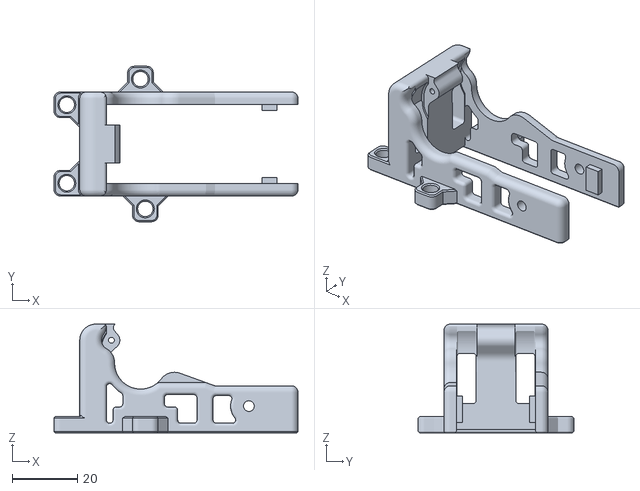
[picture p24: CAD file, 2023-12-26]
STL(Beta)/ERCF V1.0/Beta5.2/Servo_Mount_Hinge.stl
75.0 x 47.8 x 33.5

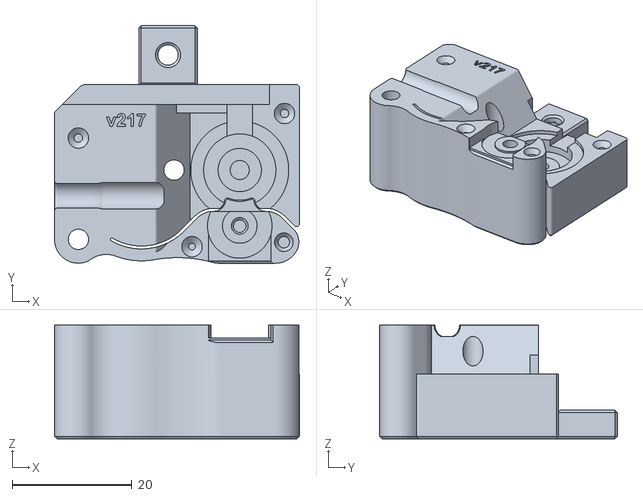
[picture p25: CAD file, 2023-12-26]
STL(Beta)/ERCF V2.0 (UNTESTED!)/Beta5.2/Encoder/623 Bearing/623_Encoder_Left.stl
41.0 x 39.7 x 19.0

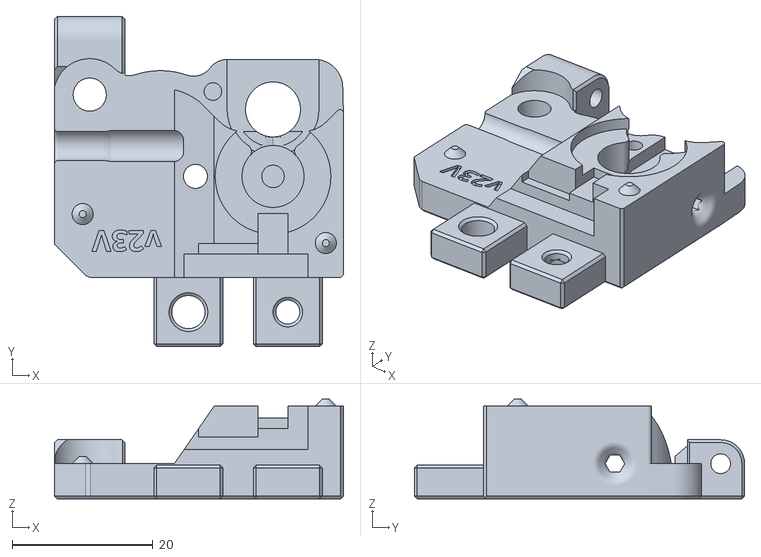
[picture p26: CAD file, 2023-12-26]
STL(Beta)/ERCF V2.0 (UNTESTED!)/Beta5.2/Encoder/V Bearing/V_Bearing_Encoder_Right.stl
41.0 x 46.8 x 14.2

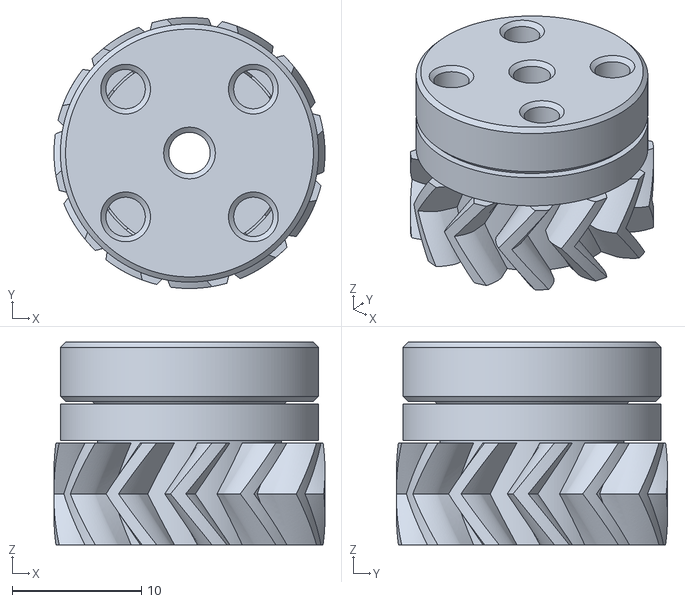
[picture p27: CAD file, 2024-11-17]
STL(Beta)/Servo_Gear_M3.stl
21.0 x 21.0 x 15.7

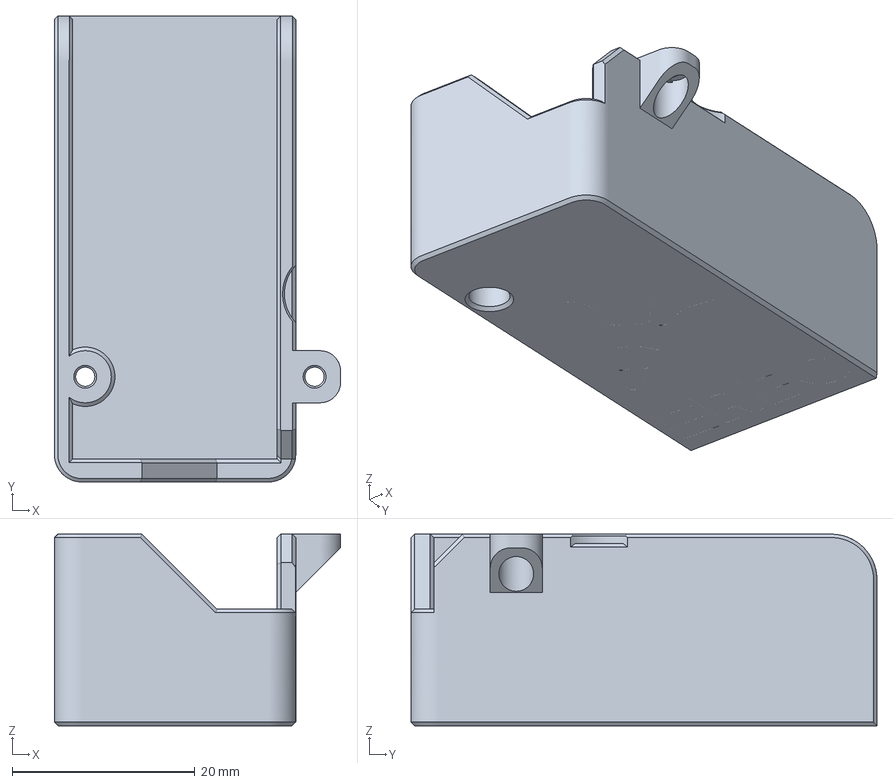
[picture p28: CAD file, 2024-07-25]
STL(Beta)/Tip Collector/Tip_Catcher_MMU.3mf
31.3 x 51.0 x 21.0 mm

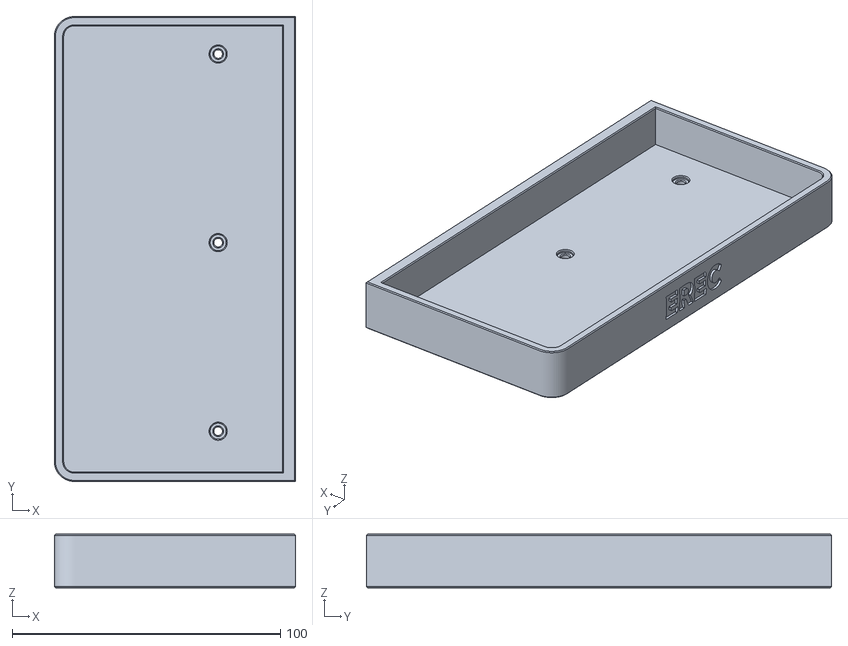
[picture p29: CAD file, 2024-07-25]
STL(Beta)/Tip Collector/Tip_Collector/7CH_Tip_Collector.stl
90.0 x 173.4 x 20.0

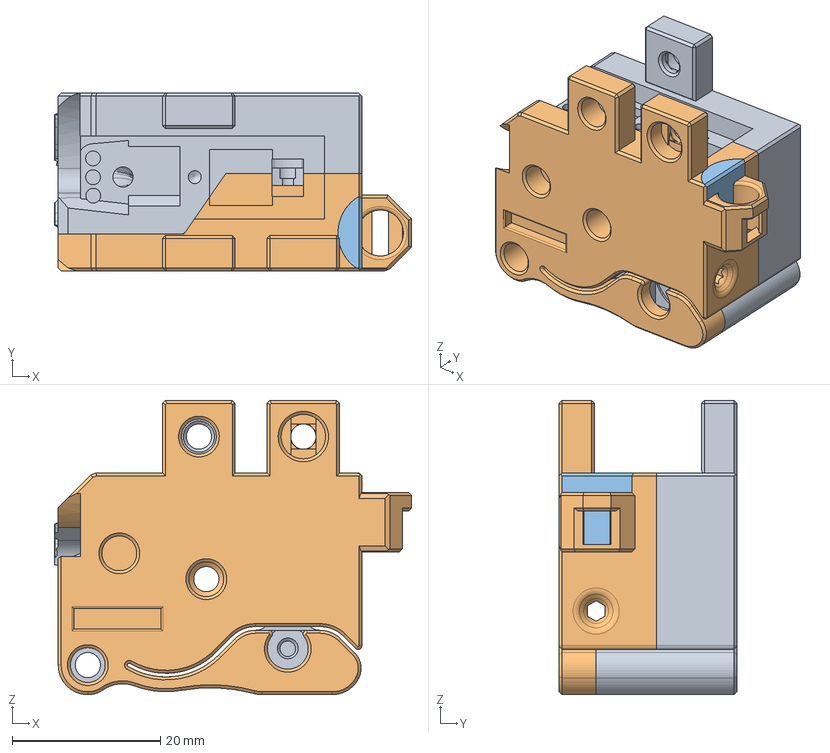
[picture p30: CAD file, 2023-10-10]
CAD/BinkyFilamentCutter_beta1.2.step
48.2 x 24.0 x 39.8 mm
Encoder_Left
Encoder_Right_with_magnets
Encoder_Right

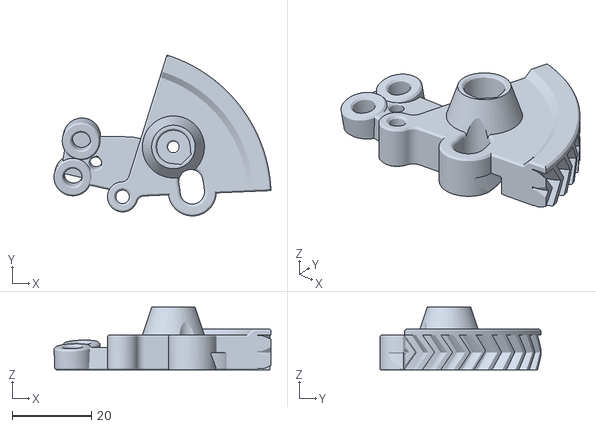
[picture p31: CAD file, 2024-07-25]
STL(Beta)/0.16_Cutter_Arm_ECAS_Closed_[a].stl
54.8 x 40.6 x 15.9

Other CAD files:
STL(Beta)/ERCF V2.0 (UNTESTED!)/Beta5.2/Servo_Mount_Hinge.stl
STL(Beta)/Encoder/623-Bearing/623Encoder_Left.stl
STL(Beta)/Encoder/V-Bearing/VEncoder_Left.stl
STL(Beta)/ERCF V1.0/Beta5.2/Encoder/Binky_Encoder_Right_With_Magnets.stl
Archive/Beta5 or older/CAD/ERFC V1.0/old/BinkyFilamentCutter_beta1.1.step
Archive/Beta5 or older/CAD/ERFC V1.0/old/BinkyFilamentCutter_beta1.step
Archive/Beta5 or older/STLs/ERCF V1.0/Beta1.2/Encoder_Binky_Cart_Left.stl
Archive/Beta5 or older/STLs/ERCF V1.0/Beta1.2/Encoder_Binky_Cart_Right.stl
Archive/Beta5 or older/STLs/ERCF V1.0/Beta1.2/Encoder_Binky_Cart_Right_With_Magnets.stl
Archive/Beta5 or older/STLs/ERCF V1.0/Beta1.2/Encoder_Cart_Left.stl
Archive/Beta5 or older/STLs/ERCF V1.0/Beta1.2/Encoder_Cart_Right.stl
Archive/Beta5 or older/STLs/ERCF V1.0/Beta1/Encoder_Blinky_Cart_Left.stl
Archive/Beta5 or older/STLs/ERCF V1.0/Beta1/Encoder_Blinky_Cart_Right.stl
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

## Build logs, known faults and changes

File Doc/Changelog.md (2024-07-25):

# EREC - Changelog 🥕

### 15/02/2024: Beta7 Release 🥕
**NOTE: Beta7 drops support for 90 degree servos!** <br>
During testing I found out that a 4:1 gear ratio is the best balance between gear size and cutting performance. Older versions of EREC had a 2:1 gear ratio which still was too weak for some special filaments ;)

- New double-helical gearing system to prevent vertical flexing during cutting moves
- New 4:1 gear ratio for even more cutting power
- M3 Heat-set insert to hold filament better in place
- Stiffer servo mounting to prevent flexing
- Encoder rail to support `Cutter_Arm` during cutting
- New mounting for the `Servo_Gear.stl`
- Even more improved knife mounting
- Angled knife for better cutting performance
- Support for PC4-M10 bowden couplings
- Added filament guide to prevent cut pieces from scattering
- Added zip tie holes for better wiring
- First official tip collector! 😉
- Overhauled documentation for easier assembly
___
### 15/02/2024: Beta6 Release 🥕
**NOTE: Beta6 drops support for the old ERCFV1**
- Helical gearing with a higher module to prevent slipping
  From my testing the gears work a lot better then the Beta 5 ones, had not a single slip during my testing
- Moved servo a bit up to fix issue #8
  The new ERCFV2 Encoder changed a bit compared to the original Binky, this required a repositioning of the gears.
- Added lock nut to the pivot to prevent the screw to be loosened over time
- Made whole construction stronger to prevent flexing
- Improved knife mounting
  I'm still not sure about this one, feel free to give your honest opinion about this https://github.com/kevinakasam/ERCF_Filament_Cutter/issues/6
- Made transition between encoder and arm smoother
- Adjusted mounting to be rotated up to 100 degree when loosened
- Improved ECAS mount
- Moved heated insert of encoder 4.5a slightly inward to prevent breaking
- Added some washers
- Added carrot 🥕
- New Logo
___
### 12/03/2024: New primary contributor 🥕
- Considering my other ongoing [projects](https://kevinakasam.com/), I’ve decided to appoint u/[BioKeks](https://github.com/BioCookieYT) as the new primary contributor to this project.
___
### 23/12/2023: ERCF2.0 Release
- Adaption for the new ERCF2.0 Encoder - made by u/[BioKeks](https://github.com/BioCookieYT)
___
### 03/11/2023: Beta5 Release
- Overhauled the cutter design for more cutting power and reliability
- Adaption of the Binky encoder for Beta5 - made by u/[BioKeks](https://github.com/BioCookieYT)
___
### 10/10/2023: Bowden Tube Adjustment
- Improved bowden tube fit by adjusting the encoder - Thanks for the feedback u/[xF4m3](https://github.com/xF4m3)
- Fixed an overhang issue with the `Encoder_Cart_Left.stl` - made by u/[BioKeks](https://github.com/BioCookieYT)
___
### 01/10/2023: [Triple-Decky](https://github.com/gneu42/Triple-Decky/tree/main) Support
- Adaption of the Binky encoder for the 3PS version - made by u/[BioKeks](https://github.com/BioCookieYT)
___
### 30/09/2023: Binky Support
- Adaption of the Binky encoder for the cutter - made by u/[BioKeks](https://github.com/BioCookieYT)
- Fixed an overhang issue with the `Servo_Mount.stl`

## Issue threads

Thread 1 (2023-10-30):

Binky

Wolffy00, 2023-10-30:
Encoder slotted wheel and push tool are missing,or link to original binky

BioCookieYT, 2023-10-30:
Hi, since the wheel and the push tool haven't changed with the adaption it isn't worth including them into our cutter repo. You can find the original Binky [here](https://github.com/mneuhaus/EnragedRabbitProject/tree/main/usermods/Binky/STL) ^^

Closed 2023-10-30.

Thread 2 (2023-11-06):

Servo Hinge missing clearance

mobilemcclintic, 2023-11-06:
The servo hinge piece on B5 is missing a clearance cutout for the slide bearing stop(?).  This forces one side of the servo hinge to bend around it.
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

juliusjj25, 2023-11-20:
Ran into this same issue, created a part with clearance.
[Servo_Hinge_Mod.zip](https://github.com/kevinakasam/ERCF_Filament_Cutter/files/13417989/Servo_Hinge_Mod.zip)

BioCookieYT, 2023-12-24:
Hi,
sorry for the late response and thanks for the feedback, I already opened a branch for this issue, going to work on a solution for this in a bit.

BioCookieYT, 2023-12-24:
Fixed with commit [58bf14c](https://github.com/kevinakasam/ERCF_Filament_Cutter/commit/58bf14c38e6058d93c8e38f4ddca13f30d7998c8)
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

Closed 2023-12-24.

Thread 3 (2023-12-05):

Question

Tutankamon00, 2023-12-05:
Hi, i have to print beta 5.1 or beta 5.2?

BioCookieYT, 2023-12-24:
Hi,
Sorry for the mess with the files, I am doing some sorting in a bit. The newest version is 5.2, if something is missing in the files use it from 5.1.

Closed 2023-12-24.

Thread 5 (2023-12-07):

Work but...

Tutankamon00, 2023-12-07:
It Work, but :
1: I think it is not reliable, because plastic hole hold the cutter arm break with time
2: Movement and mechanical assembly of cutter arm is not stable, it shake during operation
3: Integration in MMU is not very good, because cutter is activated only during change filament in normal print, is best to activate it at every change of filament even not in print

BioCookieYT, 2023-12-24:
Hi,
thanks for your feedback, be aware this project is far away from a final state, we are actively working on it on our discord (under the projects section). To answer your points:
1. Yes, we are aware of this issue and already working on this. We already released a new [servo arm](https://github.com/kevinakasam/ERCF_Filament_Cutter/blob/main/STL(Beta)/ERCF%20V1.0/Beta5/5.2/Servo_Arm.stl) which uses a different mounting system. Still doing some testing to find out what works the best.
2. Could you share a video of this please? Most of our testers got it working smoothly. In the background @kevinakasam is working on a version which uses bearings, so I think it should be solved with that.
3. The macros aren't perfect and are far away from being finished. We already had contact with the Happy-Hare developer to improve it and find solutions to our problems.

Tutankamon00, 2023-12-24:
>     2. Could you share a video of this please? Most of our testers got it working smoothly. In the background @kevinakasam is working on a version which uses bearings, so I think it should be solved with that.
>
 Hi, i'am unable to make video because i have modified a little bit the gear, I don't know how to use fusion well, I did a bit of cutting and pasting to try to reduce the distance between the teeth of the two gears, this way it is more stable, I also enlarged the part on the encoder where the hole is for the servo arm, since the original one broke at that point, however I've been using it successfully for about 10-15 days, let's hope it lasts

Closed 2024-07-25.

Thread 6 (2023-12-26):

Cutter Arm mod

Tutankamon00, 2023-12-26:
Hi, i suggest to modify the cutter arm like this, to incorporate the blade...
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

kevinakasam, 2023-12-26:
How would it cut the filament if the blade part that cuts the filament is cut out/missing 🤔

Tutankamon00, 2023-12-26:
> How would it cut the filament if the blade part that cuts the filament is cut out/missing 🤔

i using it from 10 days and work, the blade part is not missing:
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

cedbossneo, 2024-01-02:
We should also incorporate a clearance for the tube, sometimes the filament blocks on the borders of it

sanpedrox2, 2024-01-31:
Stl? 😘

Tutankamon00, 2024-02-02:
> Stl? 😘

[cutterarm.zip](https://github.com/kevinakasam/ERCF_Filament_Cutter/files/14145081/cutterarm.zip)

sanpedrox2, 2024-02-02:
Nice!
Thanks mate :)

Tutankamon00, 2024-02-03:
> We should also incorporate a clearance for the tube, sometimes the filament blocks on the borders of it

Hi, please show your mod thx :)

BioCookieYT, 2024-02-15:
Thanks for the suggestion, your mod found the way in the new Beta6. Still have to update the Readme a bit and give some credits :p

Closed 2024-02-15.

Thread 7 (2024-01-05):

Filament stuck

tutankino, 2024-01-05:
Hi, some time if Blade not cut the filament go down the Blade, because Blade arm with force go up , It Need a more robust design for cutter arm movement
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

BioCookieYT, 2024-01-22:
Hi!
Sorry for the late answer, we are already working on a more robust design on the discord server. KevinAkaSam had the time to try out a bearing version of the cutter, theoretically it would work better but we have to find a better way to mount the bearing. Even with the tightest press fit the bearing slides out after some time.
Could I ask you what Filament you tried cutting? Softer materials should work with the current design.

Tutankamon00, 2024-01-22:
I use pla+ sunlu and normal pla, with pla+ less problem, is bit soft compared to normal pla

BioCookieYT, 2024-02-15:
Hi again,
I reworked the cutter design a bit, could you please try out the new Beta6 and see how it goes now?
Thanks

Tutankamon00, 2024-02-15:
> Hi again, I reworked the cutter design a bit, could you please try out the new Beta6 and see how it goes now? Thanks

New Cutter Arm and Servo Arm for beta6 are compatible with beta5? i have ercf V1 with binky

Closed 2024-07-25.

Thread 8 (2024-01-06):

Cutter_Arm collides with Servo_Mount

24Tigger24, 2024-01-06:
Hi, the Cutter_Arm collides with the Servo_Mount in the V2.0
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

BioCookieYT, 2024-01-22:
Hi!
Sorry for the late answer and thanks for reporting this, I will work on a solution ASAP. It's a bit difficult time wise at the moment.

BioCookieYT, 2024-02-15:
Please try the new Beta, it should be fixed now. Still have to update the Readme a bit and give some credits :p

iamnotahippy, 2024-02-15:
I have printed the beta6 stls, and while I don't have my cutter wired up yet, the cutter arm no longer collides with the mount, and the gears no longer climb up one another when they encounter the resistance of cutting the filament. Also, I appreciate tapering the hole of the filament path through the cutter arm. I had to make the same modification to mine earlier to prevent jamming. Excellent work all the way around!

Closed 2024-02-15.

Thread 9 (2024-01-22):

Macro CUTTER_ACTION called recursively

pmyrie, 2024-01-22:
hi, after updating happy-hare to 2.4 every time theh cutter action is call i get,

An issue with the MMU has been detected whilst out of a print
Reason: Error running _MMU_POST_UNLOAD: Macro CUTTER_ACTION called recursively.

BioCookieYT, 2024-01-24:
Hi,
gonna find a solution ASAP. Please use HHv2.3 if possible

Raabi91, 2024-01-25:
> hi, after updating happy-hare to 2.4 every time theh cutter action is call i get,
>
> An issue with the MMU has been detected whilst out of a print Reason: Error running _MMU_POST_UNLOAD: Macro CUTTER_ACTION called recursively.

please upload you klipper log

pmyrie, 2024-01-25:
Hi sorry for the delay.

[klippy.log](https://github.com/kevinakasam/ERCF_Filament_Cutter/files/14058736/klippy.log)

Tutankamon00, 2024-01-28:
Any news? because this i 'am unable to use ercf, it go in pause and not resume
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

moggieuk, 2024-01-28:
Kevin,  the issue is that `MMU_EJECT` should not be called from within the `_MMU_POST_UNLOAD` macro because that will cause the recursive callback (yes, it just happened to work previously but should not have. lol).

The fix is to replace `MMU_EJECT` with `_MMU_STEP_UNLOAD_GATE`

So that the individual step of unloading the gate is called, not the whole unload sequence.

Tutankamon00, 2024-01-28:
I tried the Moggieuk solution and work perfect, thank you :)

BioCookieYT, 2024-01-28:
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

Thank you so much for helping out! I update the Readme in a bit.

Closed 2024-01-28.

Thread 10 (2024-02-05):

No issue

sanpedrox2, 2024-02-05:
Great work :)

i built one for my ercf v1 and it went from an unrealiable mess to more or less 100% reliable after installing the cutter.
the biggest problem i had was forming consistent tips, wich now is less important.

i did have to tweak the servo arm a bit though, the gear didnt quite reach the cutter arm gear and would sometimes skip gears.
so i extended the gear by 1mm out from the arm. now they lock nicely together.

probably my printer tolerances fault though, or the fact i printed it in petg maybe.

really nice work on this, thanks a bunch! :)

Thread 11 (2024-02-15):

Support for ERCF V1.1

24Tigger24, 2024-02-15:
According to my understanding, with Beta6 ERCF V1 is no longer supported because the new Binky Encoder no longer has a magnet to open the gates. So I added the magnets back (and 0.2mm clearance between the filament blocks and the encoder) to the 623 Bearing Version.
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
[V1.1 Binky Encoder for 623 Bearing.zip](https://github.com/kevinakasam/ERCF_Filament_Cutter/files/14300721/V1.1.Binky.Encoder.for.623.Bearing.zip)

BioCookieYT, 2024-02-15:
Hi,
did you find the time to test your mod out? I would like to add it in some kind of usermods section.

24Tigger24, 2024-02-16:
I just built it but currently don't have any multifilament prints planned. If the V2.0 encoder works, then my mod also works. The only thing I changed is the magnet on the back, which I can confirm can open the V1.1 gates.

sanpedrox2, 2024-02-16:
so... if i have a v1 with binky, springy, sturdy bunny and triple decky.. i pretty much have a V2 minus some bling?
and beta 6 should work on it?

24Tigger24, 2024-02-16:
Maybe... I designed the Encoder to work with the default V1.1 Filament blocks

BioCookieYT, 2024-02-16:
> so... if i have a v1 with binky, springy, sturdy bunny and triple decky.. i pretty much have a V2 minus some bling? and beta 6 should work on it?

With all the mods it is basically already a V2, if you are still using the triple decky magnet gates try this mod, otherwise the normal Beta6 files should work just fine

sanpedrox2, 2024-02-16:
ok, sweet. just noticed i wrote the wrong block mod. i use thumper blocks :)
so i guess beta6 will work just fine as is for me then

24Tigger24, 2024-02-17:
I added the V-Bearing Version of the Encoder and removed the clearance i needed
[V1.1 Binky Encoder for EREC.zip](https://github.com/kevinakasam/ERCF_Filament_Cutter/files/14320109/V1.1.Binky.Encoder.for.EREC.zip)

BioCookieYT, 2024-02-22:
Hi again,
Do you know how to do Pull Requests on GitHub? I made a little [Usermods](https://github.com/kevinakasam/ERCF_Filament_Cutter/tree/main/Usermods) section in the repo, similar to the VORON usermods. I would like to add some mods for EREC there ^^

24Tigger24, 2024-02-23:
I don't know completly understand what pull requests are but yes, do so.

ntchris, 2024-06-30:
I am using ERCF system V1.0, but with binky style optical decoder.
I tried the Beta6 with beta6 encoder case, it works well.
so maybe do not say "beta6 dropped support" for ERCF1, hopefully more people still using ERCF1 can use this useful cutter addon.

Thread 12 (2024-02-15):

Suggestion

Tutankamon00, 2024-02-15:
Hi Pease modify a little the design, make the teeth of servo arm wider, to maximize the contact surface with cutter arm, this increase the stability and the durability :)

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

24Tigger24, 2024-02-25:
I haven't tried it yet
[Wider Servo Arm.zip](https://github.com/kevinakasam/ERCF_Filament_Cutter/files/14396845/Wider.Servo.Arm.zip)

Tutankamon00, 2024-02-25:
> I haven't tried it yet [Wider Servo Arm.zip](https://github.com/kevinakasam/ERCF_Filament_Cutter/files/14396845/Wider.Servo.Arm.zip)

Nice thank you, i'm try to adapt for ercf 1.1 with binky, if is possibile at least only for cutter_arm and servo arm you can share .f3d with history, because this new teeth design is very difficulty to mache mod without history, thank you very much

Tutankamon00, 2024-02-25:
i checked the step of wider servo arm, but you have make it wider in the wrong direction
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

24Tigger24, 2024-02-25:
the cutter arm in your CAD is in the wrong position. You have to move it down.

My v1.1 ERCF in CAD:
[my ERCF v1.1.zip](https://github.com/kevinakasam/ERCF_Filament_Cutter/files/14397229/my.ERCF.v1.1.zip)
(.f3d-file is to large for github)

Tutankamon00, 2024-02-25:
> the cutter arm in your CAD is in the wrong position. You have to move it down.
>
> My v1.1 ERCF in CAD: [my ERCF v1.1.zip](https://github.com/kevinakasam/ERCF_Filament_Cutter/files/14397229/my.ERCF.v1.1.zip) (.f3d-file is to large for github)

YES you are right, i have to move down, thank you very much

BioCookieYT, 2024-07-25:
See Beta7 ;)

Closed 2024-07-25.

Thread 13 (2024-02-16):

config problem

mickael13160, 2024-02-16:
good evening, I have the latest happy hare v2.4, I created the cutter macro add cutter action my when I launch a print when changing filaments I have error messages with the tip cut macro I have to  disable thanks

BioCookieYT, 2024-02-16:
Could you please share the error you get? Thanks

mickael13160, 2024-02-18:
hello here are the error messages

-Tip forming performed by slicer but 'slicer_tip_park_pos' not set
-Move exceeds maximum extrusion (8.762mm^2 vs 5.000mm^2)

Thanks for your help

TheBlackMambata, 2024-05-26:
I've got something similar... I was wondering if we have to change the variable blade position too...

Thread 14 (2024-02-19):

Not an issue :-) Just an FYI and some thoughts

moggieuk, 2024-02-19:
I love the rework of this design for ERCFv2!  Just letting you know that I'm proposing to add the basic macro support for this into Happy Hare v2.5.0 release .    I'll send a DM on how to access a preview of that release.

Note that I have changed the arrangement of pre-canned macros with HH.  This would require just a little update to your doc (I have added explanation in the v2.5.0 release cfg...)

Also, and this is a little hush hush we are working with some MCU board builders to have two servos by default!  This will make this even easier to support.

Few recommendations and thoughts:
- Use `_MMU_STEP_MOVE ...` instead of `MMU_TEST_MOVE ...`.  They achieve the same thing but the former is the correct way to include in "sequence" macros and will omit debugging output
- Use the INTERVAL option to the mmu_servo ... alleviates the need to turn servo off and eliminates chance of kickback
- Not sure that the `G4 P0` are necessary
- On the idea of a "blocked" homing step....
  - The encoder is always prone to 1-2mm of error, but if an MMU had a gate sensor then this would be closer to 0.5mm
  - Trying to detect the blade in the blocked position would likely add a lot of unreliability IMHO. The "collision" detection of extruder in HH is really a hack..
  - I wonder if the inaccuracies you see could be improved by not releasing the ERCF servo until after the cut.  I believe now it will release before the _MMU_STEP_MOVE (or MMU_TEST_MOVE) cause it to go down again.  I can probably safely make the servo up after the POST_UNLOAD macro runs... let me know

Can't wait to try...

moggieuk, 2024-02-19:
Proposed macro rework:

[mmu_erec_cutter.txt](https://github.com/kevinakasam/ERCF_Filament_Cutter/files/14330675/mmu_erec_cutter.txt)

BioCookieYT, 2024-07-25:
Thanks again for your help <3

Closed 2024-07-25.

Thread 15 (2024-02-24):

macro check

Tutankamon00, 2024-02-24:
Hi please add a check before cut filament:
Check if filament is detected in encoder, if not cut, else not cut because filament loaded

This because i already have this scenario, filament inside encoder and loaded(for error on unload or other cause) and cutter try to cut and ruin filament and some time skip teeth in servo_arm/cutter_arm

Closed 2024-07-25.

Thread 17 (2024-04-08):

Servo issues and Blade mount

PaulMellor, 2024-04-08:
Unsure if it is just my setup or the servo, but it seems that the open and closed servo positions are reversed. When the current implemntation via HH it seems that I have a few issues, firstly when I power on the printer, the serve is locked in position against the arm/bracket causing it to heat up and get extremely warm.
Second issue not sure if it is the HH or the changes bade to the design, but it seems that the when I run the open or closed positions they are operate to where it should be.

iamnotahippy, 2024-04-09:
Could you upload or paste your mmu_erec_cutter.cfg?

Closed 2024-07-25.

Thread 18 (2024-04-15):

Would this servo work as substitute?

GTreaper, 2024-04-15:
Having hard time finding the specific servo mentioned
.
Link to Amazon

diymore 20kg High Pair Digital Servo Motor Full Metal Equipment Servo Waterproof for RC Car Helicopter DIY Aircraft, 270° Control Angle [Only Suitable for People Over 16 Years] https://amzn.eu/d/i6kwR9f

BioCookieYT, 2024-04-26:
According to the specs it has 20kg.cm power which should be enough to cut PLA/ABS and even harder materials like CF stuff. I would just try it out and see how it goes.

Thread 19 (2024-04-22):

movable blade attachment

dru0, 2024-04-22:
The blade is too shallow, after the first use it shifts and does not cut properly. I suggest adding a m3 screw at the bottom instead of the m2 screw and a deeper recess. At mine I did so and now it works correctly.
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

BioCookieYT, 2024-04-26:
Good idea!

Some of our testers used some M2 heat inserts to secure the knife better, an M3 screw might be better.

BioCookieYT, 2024-07-25:
See Beta7 ;)

Closed 2024-07-25.

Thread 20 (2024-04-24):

Wiring Diagram?

spikeon, 2024-04-24:
Hey guys.

I'm looking at the documentation and I can't tell where exactly I'm supposed to plug what in to what.  If you could put together a couple of sentences or a diagram of how to attach the electronics of this to the rest of the ECRFv2 system (or point me at the documentation I didn't see), I would greatly appreciate it.

Thanks!

BioCookieYT, 2024-04-26:
Noted! Working on it

What board are you using? In case you are using the BTT MBB, I would just follow the ERCFV2 manual and use at the end a free pin of [STPx](https://github.com/bigtreetech/MMB/blob/master/Hardware/MMB%20CAN%20V1.0-Pin.jpg?raw=true) . According to our testers the board has plenty enough power to supply the cutter servo.

spikeon, 2024-04-26:
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

Yes, I'm using the BTT MBB.  Does that mean I don't need this buck converter thingy I bought?

BioCookieYT, 2024-04-26:
Some people are using the BTT MBB 5V supply without any problem but I would recommend using still a buck converter for now at least, I will try to contact BTT and hear their thoughts on this topic. So connect it like this

Servo Data Pin -> Some free STPx pin
Servo + -> Buck converter +
Servo - -> Buck converter  -
**DON'T FORGET TO ADJUST THE VOLTAGE OF THE CONVERTER BEFORE CONNECTING THE SERVO!** The needed voltage is on the spec sheet of the servo, usually around 5-7.5V

spikeon, 2024-04-26:
Yeah, I figured that I'd screw that up so I bought a buck converter that outputs 5v.

https://www.amazon.com/dp/B01NALDSJ0?ref=ppx_yo2ov_dt_b_product_details&th=1

I don't trust myself with "If you set this dial incorrectly you destroy expensive things"

spikeon, 2024-04-26:
Speaking of the buck converter, do you have a recommended place to put it?  I was thinking about modifying the housing of the ERCFv2 BTT MBB to be a bit thicker so I could mount the converter to the inside of it.  But maybe printing it it's own housing and then gluing it to the outside would be better.

ntchris, 2024-06-29:
agree
should add at least one line of description to somewhere about how to connect the servo signal pin to ercf controller board.
so hopefully it should be too much work.
for example "for BTT MBB, follow the ERCFV2 manual and use one free pin of [STPx]" is a good direction
thanks.

BioCookieYT, 2024-06-30:
Sorry guys for the long waiting, Beta7 is way more work than expected :p
I quickly added a short explanation of the wiring in the Readme. Beta7 will have a proper wiring guide in the documentation.

ntchris, 2024-07-01:
Thanks for the super quick update!
I just finished the build today and did some servo test and check the BTT schematics, have some interesting finding, hopefully this could help other people have similar problems or future document.

At the beginning the servo doesn't move at all,  I spent some time to investigate using multimeter, signal generator, oscilloscope and have some finding.

1 A standard RC motor like MG996R usually require 5V signal input, and it sometimes accept slightly lower voltage signal as low as 2.9V, your mileage vary a lot by the seller/manuafurer/batch etc.  Unfortunately for BTT MBB CANbus ERCF board, all STP port are directly connected to the MCU STM32, therefore, all port has only 3.3V (at the very most) signal level, and some port has lower like 2.6V only. measured by scope.

2. Not all STPX port are made equal.  Some STPX pin has higher voltage signal output than others.
So with the out of standard signal voltage, we are only on luck, it's just lucky that the servo accepts the lower out of spec low voltage signal and works. I measured a few ports using a oscilloscope, some has low voltage as low as 2.6V output signal (ie PB8) and the servo doesn't accept or move at all, really, it's too low.

3. My BTT board, the last STP11 (PB2) output 3.3V, and the servo works very well.   Your mileage may vary.  So it's a good idea to check a few more STP port to find a better one.

4. Double check BTT's pin diagram and get the latest version, some version has PIN error.

5. On the whole BTT ercf board, there is **ONLY One** servo port has signal output of 5V, that is the **selector servo**, because BTT spent extra cost to put a signal level translator/level shifter attached to it  74LVC1G17, because ERCF originally has only ONE servo, the selector push down servo.

6. If we want to take luck out of the equitation, we may need to add a cheap level shifter (for signal) a long with a DC DC buck converter (for power). shouldn't be too difficult to connect

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

ntchris, 2024-07-01:
all stop pins are directly connected to stm32 gpio
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

BioCookieYT, 2024-07-20:
Thanks a lot for your analyses,
for now I leave the wiring guide like this. I know it isn't optimal but it will do the job for now. Thinking about a custom adapter board to shift the logic level for the future.
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

f00d4tehg0dz, 2024-08-14:
Has anyone been successful in using the Easy BRD? If so do you have a diagram handy? I cannot for the life of me get the servo gear to rotate through the PA7 data/signal pin

Blendan1, 2024-08-15:
> Has anyone been successful in using the Easy BRD? If so do you have a diagram handy? I cannot for the life of me get the servo gear to rotate through the PA7 data/signal pin

I used the extra connector to connect the servo and got the lower from an external 12/24 to 5v converter.

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

My wiring is a bit of a mess, but it works

f00d4tehg0dz, 2024-08-15:
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

Thank you!
It's odd, but mine has the same wiring and triangle labs board, yet mine won't spin the gear. (I've tried two boards now)  Is your pin the same with the same pulse width?

`[mmu_servo cut_servo]
pin: mmu:PA7			# Extra Pin on the ERCF easy Board
maximum_servo_angle: 180	# Set this to 60 for a 60° Servo
minimum_pulse_width: 0.0005	# Adapt these for your servo
maximum_pulse_width: 0.0025	# Adapt these for your servo
`

Blendan1, 2024-08-15:
I'm currently not at home, so if it's fine I will get back to you on Sunday/Monday when I'm home again. I'm not sure what my config was again 😅

f00d4tehg0dz, 2024-08-27:
> I'm currently not at home, so if it's fine I will get back to you on Sunday/Monday when I'm home again. I'm not sure what my config was again 😅

Just checking in if you ever had a chance to look? I still cannot get mine to work! Crazy.

Blendan1, 2024-08-27:
@f00d4tehg0dz sorry I  forgot, here's my config:
```
##########################################################################################
# The servo hardware configuration. Change the values to your needs.
#
[mmu_servo cut_servo]
pin: mmu:PA7			# Extra Pin on the ERCF easy Board
maximum_servo_angle: 180	# Set this to 60 for a 60° Servo
minimum_pulse_width: 0.0005	# Adapt these for your servo
maximum_pulse_width: 0.0025	# Adapt these for your servo
```
my wiring is as in the Picture.

Maybe your servo is bad, try using the selector serve (or a different known good servo), if that dosn't work on this pin with the right config then maybe you have tow bad boards.

Otherwise could you send a picture of your board where the servo is pluged in, just in case something is wrong there. any maybe a sanity check if your using the right wires.

Oh and have you checked if your 12v/24v to 5v converter is good?

Sorry if I'm saying stuff that is obvious here, but i just want to make sure nothing is missed.

f00d4tehg0dz, 2024-08-27:
> Oh and have you checked if your 12v/24v to 5v converter is good?

It's funny you mentioned that. I recently bought a new 12v to 5v converter with a display, but I couldn't get it to work correctly. It turns out I had my In/Out reversed. After correcting the issue, the motor is spinning when entering the cutting commands.

Thanks so much for the sanity check here!

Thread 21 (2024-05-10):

Documentation Position Open/Close

sharpner, 2024-05-10:
Hi guys,

I am having a bit of trouble positioning the knife correctly since I am unsure about how it should move between open/close.

Should I assemble it so, that when calling _CUTTER_CLOSE it would be in this position?
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

sharpner, 2024-05-10:
ok I figured it out:)

Closed 2024-05-10.

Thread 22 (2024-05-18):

Too much bending and filament not cut properly

Blendan1, 2024-05-18:
When it cuts the filament it cuts it 95% but then just bends the rest out of the way, if I manually hold the rest straight it cuts it with ease.
So my suggestion would be to add something to hold the filament in place or to push against. It doesn't have to be completely straight, just 40° off would work too.

Also the servo mount twists and flexes a lot while cutting (that may be because of the filament bending out of the way)

iamnotahippy, 2024-05-18:
Have you printed the newest EREC parts? They should address all of the issues you're having: the mounting frame is stiffer, and there is an m3 heatset included in the encoder housing to act as an anvil for the blade to cut against. You can find these in the Discord channel, as they're not yet posted on the github repo.

BioCookieYT, 2024-05-20:
Hi,
could you try out the new Encoder I just pushed? It includes the heatset mod which should provide better support for the filament.

https://github.com/kevinakasam/ERCF_Filament_Cutter/tree/main/STL(Beta)/Encoder/V25

AlexKid007, 2025-01-19:
Instead of an M3 heat insert, have you thought about a M2.5 heat insert? The new beta is much better than the older one but I still have some bending with some filaments.

BioCookieYT, 2025-01-19:
That might be actually a good idea! I quickly modified the V-Encoder version for a M2.5 heatset insert. There might be some issues with the bowden tube since the heatset isn't really able anymore to hold it in place. I have **not** tested the version yet due to some time issues but I attached the files in case you would like to try it.
[Files.zip](https://github.com/user-attachments/files/18470522/Files.zip)

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

AlexKid007, 2025-01-21:
I will give it a try

AlexKid007, 2025-04-03:
Sorry for late replay. I printed it and tried it out. Cuts much better now.

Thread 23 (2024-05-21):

Gear movment

rufinus, 2024-05-21:
Please see this little movie: https://photos.app.goo.gl/gbCXH4ThvoQybWH8A
(yes, video doesnt have sound)

after only one cut the lever changes positions - and the angles no longer match.  on the pass through position there is play between the gears, and the gears itself can skip over.

What did i do wrong? Any hints or pointers?

TIA

ntchris, 2024-07-03:
servo  and two gears initial position/install position need adjust.
also the cut_open cut_close angle need adjust.

BioCookieYT, 2024-07-25:
Could you please try Beta7? I'm closing this issue now, reopen if the issue persists

Closed 2024-07-25.

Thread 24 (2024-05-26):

Config issues in Happy Hare 2.51

TheBlackMambata, 2024-05-26:
I think I already set up everything ok but maybe I'm missing something about the filament position and park position relating to the blade psition (and its cutting macro) maybe...
when I print something everything is ok until the first filament change and I've got this messages in the console:

00:22
[T2] < En <<<<<<<<< [Ex << (*) << Nz] LOADED 0.0mm (e:54.2mm)
00:22
Attempting to recover filament position...
00:22
idle_timeout: Timeout set to 72000.00 s
00:22
After fixing, call RESUME to continue printing (MMU_UNLOCK to restore temperature)
00:22
MMU issue detected. Print will be paused
Reason: Unload sequence failed: Error running _MMU_CUT_TIP: The value 'mmu_gantry_servo' is not valid for SERVO.
Occured when changing tool: T2 > T4

So, when the printer finish the wipe tower lines with the first filament, it goes in a position (which I think it's the park position) and it initially begins to do the unloading - loading moves (like in the form tipping, but I disabled it with "form_tip_macro: _MMU_CUT_TIP" instead of _FORM_TIP), then it suddenly gives me those messages while staying in the parking position with the filament inside the heat-throat yet.
What am I missing?

iamnotahippy, 2024-05-26:
You should keep _MMU_FORM_TIP as your tip forming macro, and instead edit:

```variable_user_post_unload_extension : 'EREC_CUTTER_ACTION'	; Executed after default logic```

in your mmu_macro_vars.cfg

TheBlackMambata, 2024-05-26:
Ok I understood what was the problem... Of course I need tip forming to unload the filament from the extruder, so i changed to _MMU_FORM_TIP and then the variable_user_post_unload_extension : "EREC_CUTTER_ACTION" do the rest.

Sorry for bothering

Thank you very much for your amazing work guys

TheBlackMambata, 2024-05-26:
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

Yeah thanks of course I needed it XD

TheBlackMambata, 2024-05-26:
Sorry if I bother,
I've got now only a minor issue and after resolve it I think I'm good to go:

I tuned every position values of toolhead sensor, extruder to nozzle etc (I had the ercf v.1.1 version so I had to customize everything manually) but the filament loading is kinda "too fast" and now I've got a huge blob during the filament change that stucks on my nozzle and then goes to the wipe tower...   I haven't got a blobifier yet.
Any suggestion?
With the same values I didn't have such a huge blob in ERCF v.1.1 but I had everything set properly on the slicer too wherease now I'm trying to follow the guides and let the HH do everything

Motalw, 2024-10-02:
I had the same problem today (Unload sequence failed: Error running _MMU_CUT_TIP: The value 'mmu_gantry_servo' is not valid for SERVO), and I found out that you need to set the "variable_gantry_servo_enabled" to false then you can use the 	_MMU_CUT_TIP macro without problem.

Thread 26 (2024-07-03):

beta6 Helical gear angle change to opposite direction to cut better?

ntchris, 2024-07-03:
beta6 use helical gear which is great,
however per my understanding, with current design, the helical gear's angle in this direction(purple color), the cutter arm moves not only to one direction to cut, but also it tends to move outward away from the encoder wall by the axial force pointing outward away (away from encoder wall), therefore the filament is pulled out and has some chance not to cut properly.
If we could change the angle of the gear to opposite direction (green color), the cutter arm shall push inward to the encoder wall therefore the filament shall cut better.
I'm not 100% sure my understanding of the direction is correct thought, seems like it...

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

BioCookieYT, 2024-07-25:
I did it a bit different now with Beta7 ;)

Closed 2024-07-25.

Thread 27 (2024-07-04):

future feature consideration: to cut filament with 45degree or sharper

ntchris, 2024-07-04:
future feature consideration: to cut filament with 45degree or sharper
by no means this is an easy task, probably need redesign everything from scratch.

Is it possible to cut with an angle, 45degree or sharper?
So filament can have a sharp head or tip...

maybe it's too difficult for current design.
maybe need using two servos...? One for rotation to align holes and tube,
the other one for pushing down a cut button and knife...
very difficult design
easy for a manual 45degree cutter, but very difficult for an automatic one...which require two types of movement

BioCookieYT, 2024-07-25:
It's pretty difficult to achieve this, we already thought about this during Beta4!
Maybe with Beta8....

Closed 2024-07-25.

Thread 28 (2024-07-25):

Support for either standalone version or tradrack

salbang, 2024-07-25:
Could you please consider a standalone version which would envolve modifying the encoder block to just pass through the filament without the bearing, the bmg gear and the encoder.  The hole that the filament enters would fit an EACS to place the cutter in between the MMU (such as TradRack) and the extruder.

Another option would directly support tradrack with binky encoder mod. I have tried to mirror all the parts, but there are some issues with the dimension which blocks the Tradrack selector does not touch the endstop. Thank you.

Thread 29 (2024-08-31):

Filament bends instead of cuts

f00d4tehg0dz, 2024-08-31:
Most of the time, the filament bends instead of getting a forceable cut.  I noticed quite a bit of flex with the mount as well. Perhaps user error on my part? I'm using Beta 7 on an ERCF 1.1 Klipper 11 with Happy-Hare.

Here is my config

```
# These variables control the servo movement
variable_servo_closed_angle   : 5	; Servo angle for closed postion with bowden aligned MMU
variable_servo_open_angle     : 180 ; Servo angle to open up the cutter and move bowden away from MMU
variable_servo_duration       : 0.4	; Time (s) of PWM pulse to activate servo
variable_servo_idle_time      : 1.0	; Time (s) to let the servo to reach it's position

# Controls for feed and cut lengths
variable_feed_length          : 58	; Distance in mm from gate parking position to blade (ERCFv1.1: 58, v2/other: 48)
variable_cut_length           : 10	; Amount in mm of filament to cut
variable_cut_attempts         : 3	; Number of times the cutter tries to cut the filament```

Blendan1, 2024-08-31:
I have had the same issue before, what solved it for me was not using PTFE tubing on the encoder.

It seems that the extra squishyness of the tube allows the filament to bend, but when it directly presses against the pla it cuts.

Maybe a design change could be that a second knife, that's mounted on the encoder so that's more like a scissor.

Closed 2024-09-04.

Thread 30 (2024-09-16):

Holes M3 inserts

Soprano80, 2024-09-16:
The M3 heat set inserts holes on the encoder are too big. The holes have a diameter of 4.7 mm. My M3 heat inserts have a diameter of 4.45 mm. This means that the M3 heat set inserts fall into the holes.

iamnotahippy, 2024-09-16:
Voron standards call for m3 heat set inserts with a length of 4mm and a diameter of 5mm. You need to purchase the proper sized inserts.

Closed 2024-09-19.

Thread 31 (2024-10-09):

Calibration and documentation

dmxkov, 2024-10-09:
I guess most of the users are smart enough to figure how does it work.
Apparently I'm not that one.

1. I haven't found any information about calibration or first setup of the servo. Happy Hare has really nice docs and pics with full explanation how put the servo, which angle it should be and so on.
2. Showcase at the end of this repo has an old video with old variant how does it work. The macro has logic somehow described but not enough to make it user friendly.
3. Official link to Aliexpress has poor quality servo and should be revised at least.

Thank you in advance.

BioCookieYT, 2024-10-12:
Hi!
Sadly I am missing completely time to make a proper showcase video but I would recommend joining our discord server or ask in  the Voron discord. There are already a lot EREC users out there who could help with any misunderstanding.

For the servo could you please tell me more about it or share a video? I tested the kit and the servo was enough for any standard PLA/ABS cutting. It might be a quality issue, so its definitely something to investigate. I already contacted the vendor in case they switched servos or something.

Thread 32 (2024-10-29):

Problem with stringing

old-relic, 2024-10-29:
I have an ERCF Sturdy Bunny Binky  EREC equipped MMU on a Creality CR10S-4 with a Revo/Stealthburner hotend. the extruder has sensors above and below the extruder gear for sensing filament tip position during loading.

PLA and PETg generate stringing that plugs up the selector.  So I use MMU_FORM_TIP and standalone skinny dips to burn the hairs before retracting the filament up to the EREC cutter. The cut tips have good tips and hairs are now not a problem.

But there is a problem that occurs just after the filament does the happy dance during standalone skinny dipping. Immediately before the filament is withdrawn up the reverse bowden, a short extrude happens, about 10mm. This causes a short bit of extruded filament which gets dragged around to become attached to various print parts. I have been looking for the parameter(s) that might control this action. But have failed to find it.  Is there a parameter that controls this short extrude before filament extraction?

old-relic, 2024-11-25:
I have abandoned the EREC cutter and moved to the Filametrix cutter. The reason is that I was never able to solve the problem of getting good tip forming working. Strings and hairs caused false triggering of the extruder sensor during filament extraction.

Closed 2024-11-25.

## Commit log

2023-09-29 Initial Upload
    [Encoder_Cart_Left.stl, Encoder_Cart_Right.stl, Servo_Mount.stl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]
2023-10-01 Rename Encoder_Blinky_Cart_Right.stl to Encoder_Binky_Cart_Right_With_Magnets.stl
    It's called Binky ;)
    [Encoder_Binky_Cart_Right_With_Magnets.stl]
2023-10-01 Moved file
    [BinkyFilamentCutter_beta1.step]
2023-10-01 Rename File
    [Encoder_Binky_Cart_Left.stl]
2023-11-03 Beta5 Release
    [Cutter.stl, Cutter_Arm.stl, Cutter_Block.stl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]
2023-11-03 Binky Beta5
    Note: Untested
    [BinkyFilamentCutter_beta1.2.step, BinkyFilamentCutter_beta5.0.step, Binky_Left.stl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]
2023-11-03 Binky Beta5.1
    [BinkyFilamentCutter_beta5.0.step, BinkyFilamentCutter_beta5.1.step, Binky_Encoder_Left.stl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]
2023-11-03 Beta 5.2 release
    [CutterArm.stl, Cutter_Arm.stl, Encoder_Chart_Left.stl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]
2023-11-03 Undo Beta 5.2 release
    [CutterArm.stl, Cutter_Arm.stl, Encoder_Chart_Left.stl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]
2023-11-14 Macro and Beta Update
    [Cutter_Arm.stl, Servo_Arm.stl, Servo_Mount.stl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]
2023-11-14 Forgot to orientate the STLs
    [Cutter_Arm.stl, Servo_Arm.stl, Servo_Mount.stl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]
2023-12-08 Added 5.2 CAD
2023-12-08 5.2 CAD now with hardware
2023-12-23 ERCF2.0 Beta Update
    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
    [623_Encoder_Left.stl, 623_Encoder_Right.stl, BinkyFilamentCutter_beta1.1.step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]
2023-12-23 Removed CAD due to some issues
2023-12-23 CAD Update
2023-12-24 Added Cutout for Selector, Updated CAD, Updated ERCFV2.0 to 5.2
    [623_Encoder_Left.stl, 623_Encoder_Right.stl, Cutter_Arm.stl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]
2023-12-25 Better file sorting
    [Binky_Encoder_Left.stl, Binky_Encoder_Right.stl, Binky_Encoder_Right_With_Magnets.stl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]
2023-12-26 File sorting
    [623_Encoder_Left.stl, 623_Encoder_Right.stl, BinkyFilamentCutter_beta5.1.step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]
2023-12-26 Update CAD
2023-12-26 Revert "Better file sorting"
    This reverts commit 8a806460a32d1ba828b5b8015fee6ae268352f9f.
    [Binky_Encoder_Left.stl, Binky_Encoder_Right.stl, Binky_Encoder_Right_With_Magnets.stl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]
2023-12-26 Fixed Selector issue
    [SPRINGY_Servo_Mount_Hinge.stl, Servo_Mount_Hinge.stl]
2024-02-15 File sorting for Beta6
    [623_Encoder_Left.stl, 623_Encoder_Right.stl, BinkyFilamentCutter_beta1.1.step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]
2024-02-15 Added STLs
    [Cuuter_Arm_With_Supports.stl, Left.stl, Right.stl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]
2024-02-15 Update BOM
2024-02-16 Rename files
    [[a] Cutter_Arm_With_Supports.stl, [a] Servo_Arm.stl]
2024-02-20 Update STLs and Manual
    [Servo_Base.stl, Servo_Mount.stl, Servo_Mount_Hinge.stl]
2024-05-20 New Encoder
    [V25_Left.stl, V25_Right.stl]
2024-06-21 Archive Beta6
    [623_Encoder_Left.stl, 623_Encoder_Right.stl, BinkyFilamentCutter_beta1.1.step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]
2024-06-21 Update Base STLs
    [0.16mm [a] Cutter_Arm_ECAS.stl, Servo_Base.stl, Servo_Gear.stl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]
2024-06-21 Update Encoder STLs
    [Left.stl, Right.stl, V25_Left.stl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]
2024-07-22 Update Doc AGAIN!
    [0.16mm [a] Cutter_Arm_ECAS.stl, Left.stl, Right.stl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]
2024-07-25 Add STLs
    [0.16_Cutter_Arm_ECAS_Closed_[a].stl, 0.16_Cutter_Arm_ECAS_Open_[a].stl, 4CH_Tip_Collector.stl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]
2024-07-25 Add CAD
2024-07-25 Fix BOM
2024-11-17 Servo Gear M3 Version
    [Servo_Gear_M3.stl]
2024-11-17 Update Heatset Insert Link
2025-01-15 Added nightowl adapter usermod
    [Cover_Main_Body.stl, EREC_Adapter_Plate.stl, Magnetic_Cover_Plate.stl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]
2025-01-15 Important 🥕 Update
2025-02-05 Folder Cleanup
    [Cover_Main_Body.stl, EREC_Adapter_Plate.stl, Magnetic_Cover_Plate.stl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]
